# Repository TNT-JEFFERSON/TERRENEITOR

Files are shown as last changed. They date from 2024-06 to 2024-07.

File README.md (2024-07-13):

# `TNT` - `TERRENEITOR`

## About

This repository provides information and knowledge regarding the current progress, evolution, and development of our self-driving robot vehicle for the World Robot Olympian (WRO) 2024 competition in the category Future Engineers, which is build and coded by us.

## TNT & Terreneitor - WRO 2024 Future Engineers

The name of our team is TNT, we chose this name because we will _explode_ the comptetition with our hard work and dedication! On the other hand, Terreneitor is the name of our autonomous robot, build by using lego and arduino together. We are a group of Venezuelan high schoolers who yearn to learn and be masters in robotics. TNT also have plenty of objectives like:

* Obtain expertise and mastery in robotics, engineering and self-driven robots.
* Learning how to cooperate and work as a team to solve problems with ingenious, imaginative, and creative solutions.
* Acquire knowledge regarding new and old technologies, information about eletronics, hardware, software, and more.
* Gain experience for opportunities or competitions that we might face in the future.
* Win the competition and enjoy the process through this exciting road!

TNT is form by three members (all 15 y.o.):

  - Raffaella Salama Arias
  - Emiliana Raquel Guerrero Fermíns
  - Nicola Pasquale Simone Perdomo

One thing that defines us, TNT, is that unlike others, we _don't_ give up easily, we are determine to be the best and improve as much as possible, always looking for success and enjoying every part of the process. You can see this characteristic about us being really strong during "our journey, process and prototypes" below and in the `Older versions of our final robot` folder.

## Content

- `Pictures (Team and vehicle)`: contains photos of the final robot from different views and angles. And photos of us individually and in group.
- `Older versions of our final robot`: contains photos of our previous ideas and prototypes that eventually lead to the final design and robot, Terreneitor.
- `Obstacle management`: contains the source code of the prototypes and the final robot with detailed comments, strategies, flowchart diagrams and pseudocode.
- `Videos`: contains links to our Youtube videos which show how our previous attempts turn out and function, and also how the final robot completes the challenges and more. 
- `Mobility management`: contains all the 3D printed models we used throught our journey, all the lego pieces, electrical components, and materials used in the final robot, a brief discussion regarding the vehicle chassis design/selection as well as the mounting of all components to the vehicle chassis/structure, and more.
- `Power and sense management`: contains power and sense management about the power source for the vehicle as well as the sensors required to provide the vehicle with information to negotiate the different challenges, the reasons for selecting various sensors and how they are being used on the vehicle together and a wiring diagram with BOM that includes all aspects of professional wiring diagrams.

## Materials and components

What is Terreneitor made of? Terreneitor is made of pieces and blocks from pieces and lego parts from diverse lego sets we found in our robotics laboratory, while also using "ready to go" electrical components. We also used an Arduino board as our main controller, since this is what we learned in our school.

|THE LEGO PIECES OUR ROBOT USES ARE:|THE ARDUINO/ELECTRICAL COMPONENTS OUR ROBOT USES ARE:| 
|---|---|
|6x Yellow 4265c|1x MicroServo 9g (SG90)|
|10x Gray 3713|1x Yellow 9V Geared Dc Motor|
|33x Black 2780|1x Gray 5V Dc Motor|
|1x Red 6538c|1x Pixycam 2.1|
|1x Gray 60483|2x Ultrasound sensors|
|2x White x346| Arduino cables |
|2x Red 44809|2x Bateries|
|2x Black 32270|1x Arduino Uno Board|
|1x Blue 32523|1x Protoboard|
|1x Gray 32523|
|4x Gray 32073|
|1x Black 33299|
|4x Gray 32140|
|1x Gray 44294|
|2x Black 3707|
|2x Gray 48989|
|4x Dark gray 3648|
|4x White 40490|
|5x Gray 40490|
|6x Gray 64179|
|4x Grey 56908|
|4x Black 41897|

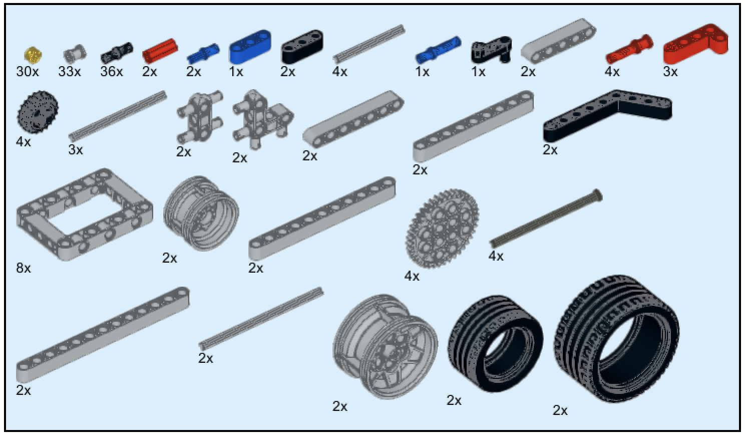
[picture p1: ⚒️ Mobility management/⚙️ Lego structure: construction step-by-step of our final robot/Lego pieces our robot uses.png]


### To know the complete list of all the materials used visit the `Mobility management` folder.

## Our journey, progress and prototypes

In the beginning of our journey, we had plenty of various and diverse ideas on how to build our robot but eventually it all worked out. When we first started, we did messy sketches and tried a lot of ideas. Here are some of our first sketches and ideas for Terreneitor:

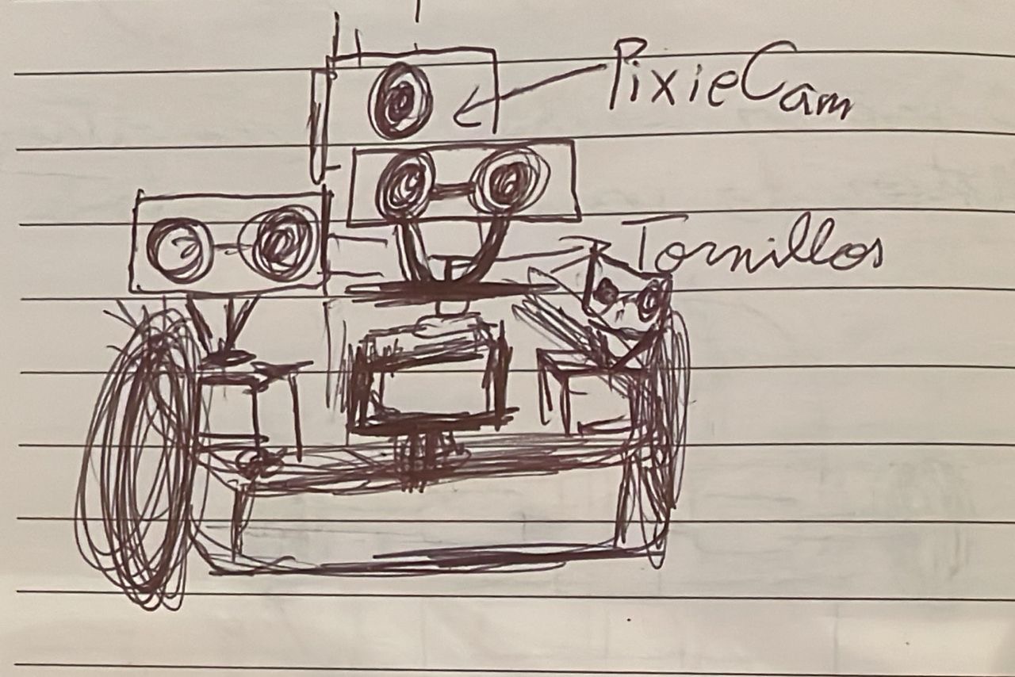
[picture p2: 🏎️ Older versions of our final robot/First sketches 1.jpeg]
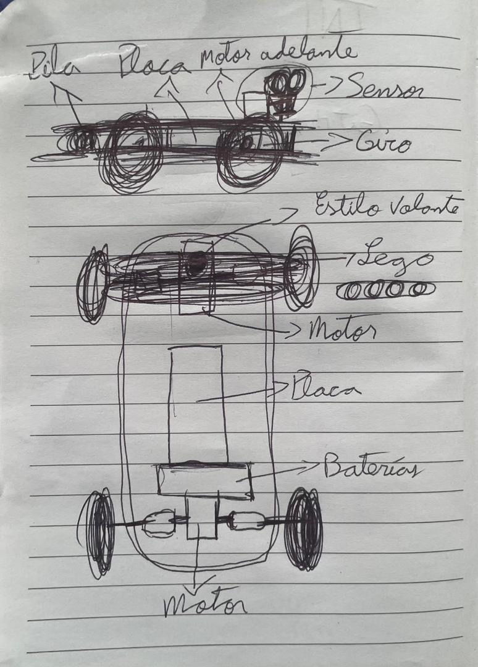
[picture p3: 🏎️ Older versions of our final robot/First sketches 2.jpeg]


Eventually, with these sketches in mind, we started working on the physical robot. We had high hopes for our first prototype, and the more we worked on it, the more our hopes grew. But, there was a problem, a big one...if you see "First prototype wheels mechanism" (you can find in the `videos` folder) you might think, like us, that it would be super fast on the ground, however when we finally were ready to put it to the test... it failed. The wheels mechanism of this prototype did not work on the ground. We tried to change many things and pieces in this prototype to see if it would help, but all our work was in vain, the mechanism still did not work on the floor. Eventually, we find out the cause... the mechanism didn't work because the dc motor that we were using, eventhogh it was fast, it didn't have enough strength and power to move the gear mechanism (the robot was also really tall and heavy causing the dc motor to be carrying this weight all the time, since it was located on the lower part of it. Let's not forget to comment that, also the mechanism for the direction of the robot did not work out too because the motor couldn't move the mechanism (for a better visual understanding visit the `videos` folder), although that was a minor problem compare to the wheel mechanism problem.

But, not everything went wrong with our first prototype because we also did a circuit for the servomotor and for the wheels, and we had a base (constructed by us with lego). All of this things helped us, along with our previous mistakes, to improve and create our second prototype.

In our second prototype, since we learned from our failures and errors from the past prototype, it didn't had any enormous problem, however, there were still problems to be fixed. We realized that the two dc motors we had weren't working simultaneously, which violated the rules of the WRO 2024 competition and also that, eventhough the mesurements of the robot were good according to the rules, it was still, to big in width, which lead to problems like being too heavy so it went super slow (which you can see in the video "Second prototype on the track" in the `videos` folder). And a third
problem was that when we building this prototype was that it did not direct the robot correctly because the wheels of the front couldn't rotate to either left or right. 

As you can realize by now we had plenty of problems since the beginning, let's gather all of them:

### First prototype:

- The wheels mechanism did not work on the ground
- The direction mechanism did not work
- Heavy
- Tall

### Second prototype:

- The mechanism we were using for the wheels violated the rules of WRO 2024 competition
- Too big in width
- Too heavy
- Slow, due to the two previous problems
- Didn't direct the robot correctly

### *(to learn more about our sketches and prototypes go to the `Older versions of our final robot` folder)*

### Final robot

Journies have downsides and good times, advantages and disavantages. After the first and second prototype you might think that because of all this problems we might give up, but contrary to this hypothesis, we didn't (after all "third time's a charm", right?), instead we improved and our mistakes made us stronger, wiser and smarter. So when we created our final robot, we made sure to not make any of our previous mistakes, being very causious in its construction. Thanks to this, we have a robot that is:

- Light weighted
- Short and thin
- The direction and wheel mechanism do work
- Fast
- Doesn't violate any rules of the WRO 2024 competition.

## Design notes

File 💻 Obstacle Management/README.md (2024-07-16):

# Obstacle management

In this directory you will find:
- the software we used to make our code
- all the code we used for our prototypes and the final robot
- our source code with detailed comments
- our pseudo code
- all the strategies our robot uses in order to complete the open challenge round and the obstacle challenge round
- our old and new flowchart diagram 

## Software

The software we used for coding and programming our robot, Terreneitor, is _Arduino Integrated Development Environment (IDE)  _ application version: 2.3.2 in MacOS. Arduino uses a variant of the C++ programming language. The Arduino Integrated Development Environment or Arduino Software (IDE)  contains a text editor for writing code, a message area, a text console, a toolbar with buttons for common functions and a series of menus. It connects to the Arduino hardware to upload programs and communicate with them. We chose using this software not only because of its simplicity but because it what we learned in our school.

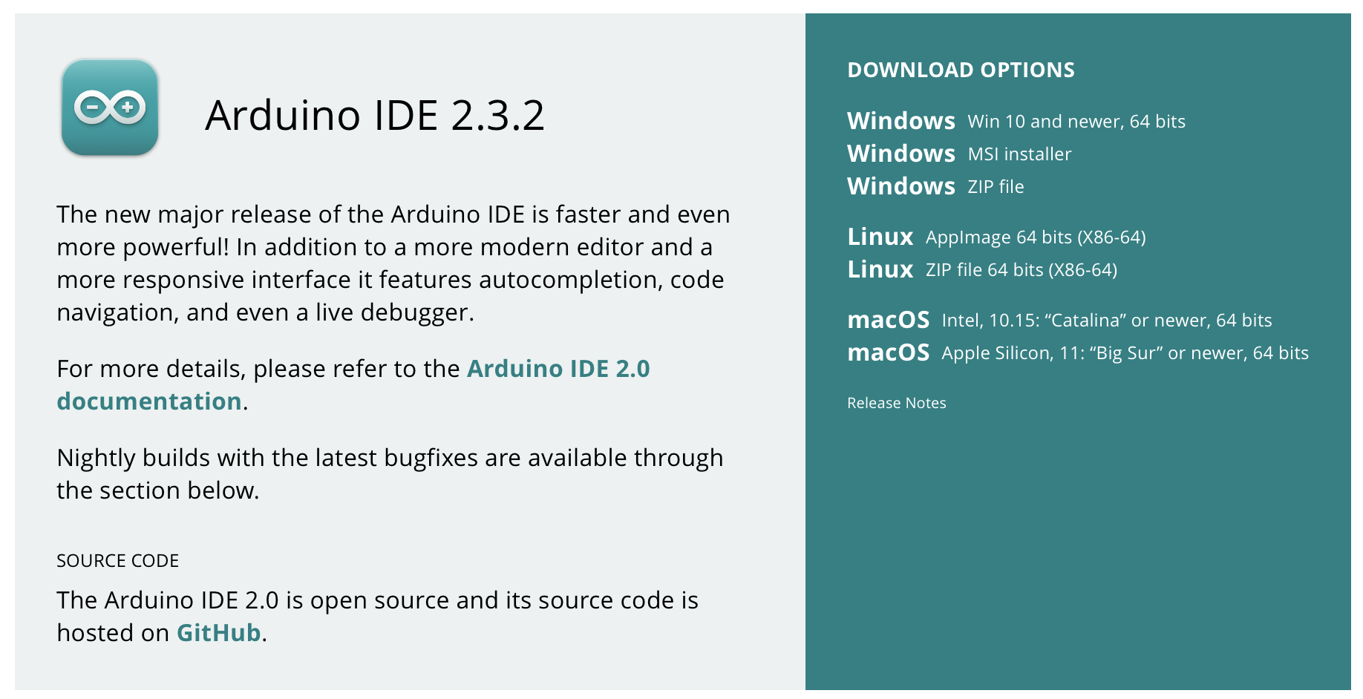
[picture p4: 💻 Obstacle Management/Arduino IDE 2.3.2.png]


##  Pseudocode and strategy

A pseudocode is a representation of code used to demonstrate the implementation of an algorithm without actually doing so. It often acts as a rough draft of coding projects, and is written in an explainable manner to be understandable by programmers at any knowledge level. Meanwhile, a strategy, in this case, is our plan to achieve our goals during the challenges and rounds of the WRO 2024 future engineers competition. Here is our pseudo code and strategy explained in detailed for each round:

### Round 1:

-  The dc motors starts and the car begins to go forward.
-  It continues going straight forward until the pixycam detects an orange or blue line in the track.
-  If the line it sees is orange, it will turn to the right.
-  If the line it sees is blue, it will turn to the left.
-  While the pixycam is working, the ultrasonic sensors in our robot are working too. These ultrasonic sensors help us know the distance between our robot and the walls in the track.
-  If the left wall is closer to the robot than the right wall, it turns to the right side, if not, then the right wall is closer to the robot than the left wall, it turns to the left side.
-  After the robot sees the orange line and/or blue line and turns 12 times (makes 3 laps) it stops where it started and the round ends, if it doesn't sees the orange line and/or blue line and turns 12 times (makes 3 laps) it constinues going until the 3 laps are completed and the round/challenge ends.

### Round 2:

-  The dc motors starts and the car begins to go forward.
-  It continues going straight forward until the pixycam detects an orange or blue line _or_ a green or red obstacle in the track.
-  If the line it sees is orange, it will turn to the right.
-  If the line it sees is blue, it will turn to the left.
-  If the obstacle it sees is red, it will turn to the right.
-  If the obstacle it sees is green, it will turn to the left.
-  While the pixycam is working, the ultrasonic sensors in our robot are working too. These ultrasonic sensors help us know the distance between our robot and the walls in the track.
-  If the left wall is closer to the robot than the right wall, it turns to the right side, if not, then the right wall is closer to the robot than the left wall, it turns to the left side.
-  After the robot sees the orange line and/or blue line and turns 12 times (makes 3 laps) it stops where it started and the round ends, if it doesn't sees the orange line and/or blue line and turns 12 times (makes 3 laps) it constinues going until the 3 laps are completed and the round/challenge ends.

### Round 3:

** In this round, the robot works the same the only step that changes in the final step in which the car has to park inside a magenta parking lot. **

-  The dc motors starts and the car begins to go forward.
-  It continues going straight forward until the pixycam detects an orange or blue line _or_ a green or red obstacle in the track.
-  If the line it sees is orange, it will turn to the right.
-  If the line it sees is blue, it will turn to the left.
-  If the obstacle it sees is red, it will turn to the right.
-  If the obstacle it sees is green, it will turn to the left.
-  While the pixycam is working, the ultrasonic sensors in our robot are working too. These ultrasonic sensors help us know the distance between our robot and the walls in the track.
-  If the left wall is closer to the robot than the right wall, it turns to the right side, if not, then the right wall is closer to the robot than the left wall, it turns to the left side.
-  After the robot sees the orange line and/or blue line and turns 12 times (makes 3 laps) it searches for the magenta parking lot with the pixycam and  parks inside it and the round ends, if it doesn't sees the orange line and/or blue line and turns 12 times (makes 3 laps) it constinues going until the 3 laps are completed and it parks inside it and the round/challenge ends.

In order to explain all of the above better, we designed a flowchart diagram, a visual representation that depicts our process, system, computer algorithm, and a brief summary of how our code of the robot works on the track. During our journey we created two flowcharts as you can see below. The difference between the two diagrams is that the old one wasn't a good flowchart and didn't completely follow all the rules of a flowchart diagram and didn't explained correctly how our code and process works, on the other hand, our new flowchart diagram, does follow all the rules and conditions of a new flowchart diagram and explains correctly how our code and process works.
 
(both diagrams were created entirely by us, TNT, using the smartdraw website: https://www.smartdraw.com/flowchart/flowchart-maker.htm)

|Our old flowchart diagram|
|--------------------------|
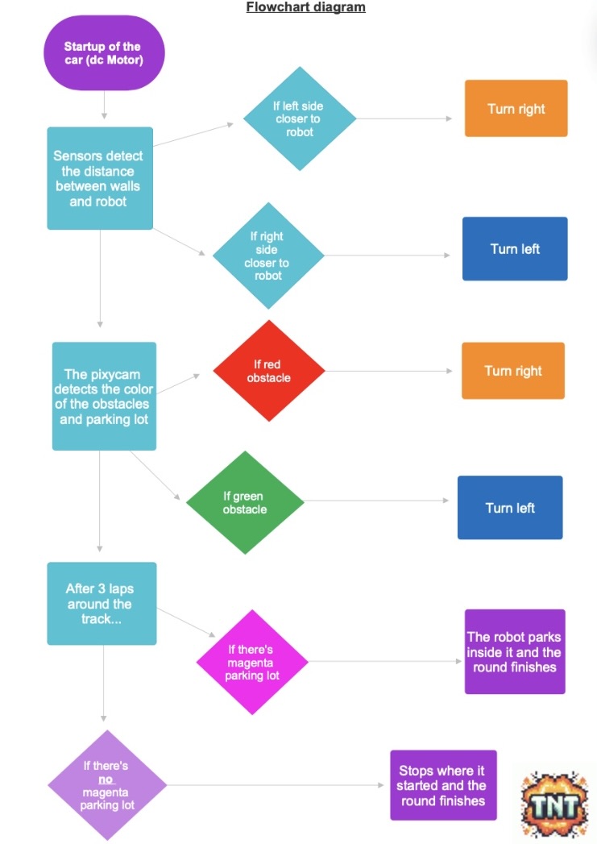
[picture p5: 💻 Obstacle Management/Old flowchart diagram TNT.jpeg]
||

|Our new flowchart diagram|
|-----------|
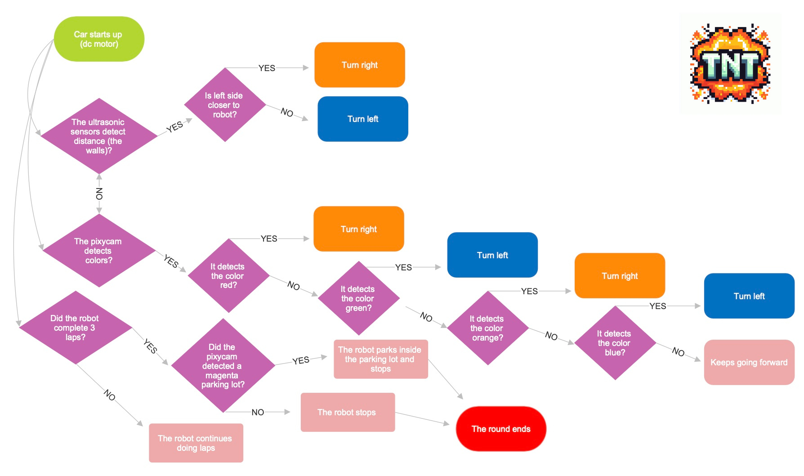
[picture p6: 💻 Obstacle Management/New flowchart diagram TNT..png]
||

In this directory we uploaded all the codes we used both for our prototytpes and the final robot. All of this source codes contain detailed comments, so make sure to check them thoroughly!

Below you have a brief summary, pseudocode and strategies used in each indivual file and code:

## Code for first round (Open challenge round)

This code works for the first round, if you want to know what it is about check the file in the folder that's named "First round.ino", since the detailed comments will tell you what it is about.

## Code for first round 2 (Open challenge round)

This code works for the first round, if you want to know what it is about check the file in the folder that's named "First round.ino", since the detailed comments will tell you what it is about.

## Code for second round (Obstacle challenge round)

This code works for the second round, if you want to know what it is about check the file in the folder that's named "Second round.ino", since the detailed comments will tell you what it is about.

## Below you'll see some _tests_ codes we did before:

## Code for the motors of the second prototype:

- What this code does is simple: 

   - First, it takes 2 seconds to start the code, this is made intencionally so we had to accomodate the robot in the track            comfortably.
   - Second, the code starts and it turns both motors on, making it go in a straight line for 14 seconds
   - After the 14 seconds have passed, the robot turns to the side for 9 seconds (by turning off one motor while the other one is still on)
   - And finally, it goes in a straight line again (turning on both motors, like in the beginning).

The robot does this cicle 4 times,for it to finish that round, which is the first challenge (the open challange). This code is a way of completing the first challenge by using time.

- You can see this code being used and putted to the test in "Second prototype on the track" (in the videos folder).

## Code for the three ultrasonic sensors:

- This code is so the three ultrasonic sensors work together in unison. The sensors perceive the distance in cm in this code.
- This code also works together with the servomotor code.

## Code for the servomotor and ultrasonic sensors:

This code makes the direction mechanism and the three ultrasonic sensors in our robot work together

It works like this:

- If the robot detects that one side is more than 50cm it goes that way
- If the robot detects that one side is less that 50 cm it goes to the opposite way

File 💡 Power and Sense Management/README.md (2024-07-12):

# Power and sense management

In this directory we will talk about:

- the power source for the vehicle
- the sensors required to provide the vehicle with information to negotiate the different challenges
- reasons for selecting various sensors and how they are being used on the vehicle together 
- wiring diagram that includes all aspects of professional wiring diagrams
- Bill Of Materials (BOM)

Terreneitor has two power sources: The first one being a 5000 mA powerbank which provides power to the Arduino Rev3 Board, which is the main controller of our robot. The second one are four rechargable batteries of around 2300-1300 mA each and 1.2V that give power to the dc motor and are connected directly to the protoboard (were it becomes part of our circuit). In order, to turn the batteries (basically the robot) on and off, it counts with a switch (a power controller board) to do this.

These power sources for the vehicle, give power to whole robot, but some really important components that it gives power to are the sensors. Our robot counts with three sensors, two ultrasonic ones and one pixycam 2.1. The ultrasonic sensors help us detect the distance between the robot and the walls and/or obstacles, these two sensors are in the front of our robot. The pixycam 2.1 helps up detect colors in the surroundings of the robot, it helps detect the red or/and green obstacles in the second challenge, the magenta parking lot, the black walls, and the orange and blue lines in the track. 

We chose to have ultrasonic sensors in our robot because since they detect the distance between the robot and the walls/obstacles it helps us know how far or how close the robot is to these things. These is important because if the robot is close to the walls, for example, it turns (you can see these better explained in our code and in the `obstacle management` folder). If our robot didn't had any ultrasonic sensors it would 100% crash with the walls or obstacles in its way and wouldn't complete the challenges correctly. On the other hand, we chose to have a pixycam in the front of the robot, to the detect the colors of the things around the robot, this is also extremely helpful and important because, for example, in the rules of the WRO 2024 competition its established that if the robot sees a red obstacle it has to turn right, if we didn't had the pixycam we wouldn't be able to know the color of the obstacles in the track and would fail the challenge.

As you can see, the sensors are a very important part in the robot and eventhough they consumed a lot of power (because we have three of them) it is super worth it. 

Of course, for pracmatiqueness and better efficiency, the sensors and the power sources are not connected directly to the our main controller, the Arduino Rev3 Board, instead, they are connected to a circuit which then connects to the board. For you to know what our circuit looks like and how it works we made a wiring diagram that includes all aspects of professional wiring diagrams, for a better comprehension:

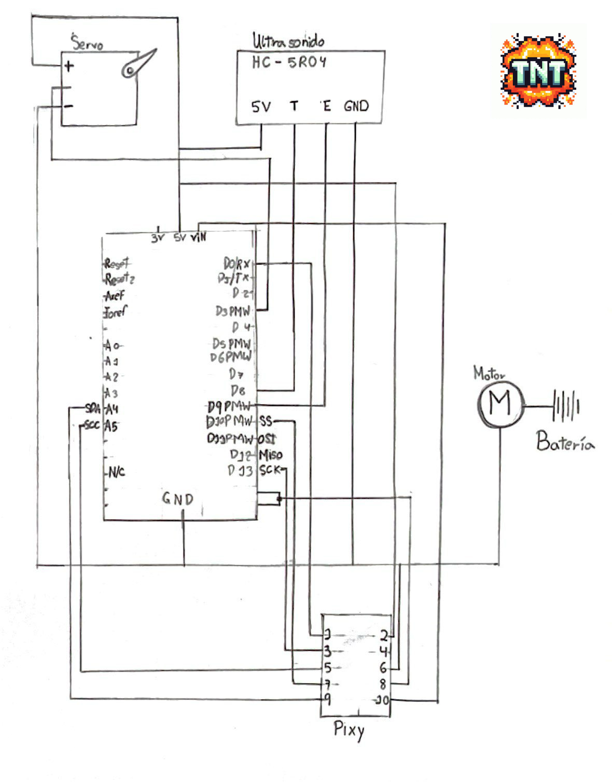
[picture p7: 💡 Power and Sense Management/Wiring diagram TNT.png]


The sensors and the power sources are not the only components and pieces we used in our robot, and are not the only important and expensive parts we used, so we also elaborated a Bill Of Materials (BOM). Below you can see it:

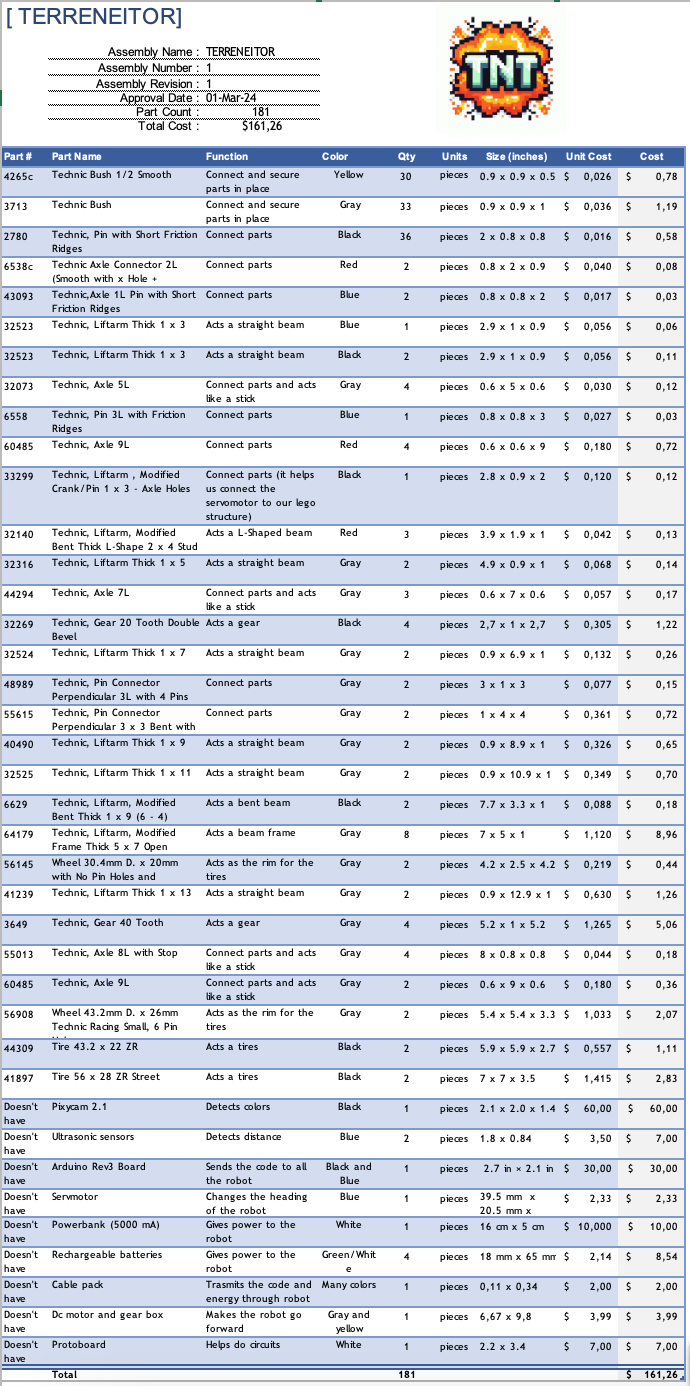
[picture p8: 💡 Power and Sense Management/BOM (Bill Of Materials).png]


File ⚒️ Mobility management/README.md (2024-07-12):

# Mobility management

We chose a vehicle chassis that was open and that would allow us to have both an Arduino board, a protoboard and a power source connected, which is why it was necessary to create two floors because otherwise the car would be very long and would exceed the measurements provided. We made two floors with simple Lego structures and made some small adaptations to place our DC motor, place our battery and 3D printed our own piece to be able to mount the pixy camera.  

We chose a 3V DC motor, which is one of the most common, but seeing that it did not have enough power, we worked with the “large gear-small gear” principle (to increase the speed of the output the driver gear is larger than the driven gear which is small (this will increase the speed of the output but decrease the “torque”)), which is what you will see in the diagram of the gear box and our propulsion, then with that engine, we simply place gears at the end of it, to double what is the angular speed and the linear speed that is generated on what are our rear wheels. That generates a little instability if we do it with a single gear, therefore we place two gears on each side, not to generate more power, but to generate more stability. 

We are working with 5000 mA batteries that are commercially known as “powerbanks” precisely because they give a stable current through a USB cable that will not bend or break and will allow us to constantly power our vehicle, we also use four rechargable batteries of around 2300-1300 mA each, to power our robot. (to see this explained in more detail check the `power and sense  management` folder)

For the direction, we had to use a servomotor, it would have been ideal to place another 3V DC motor for this function, however, we would have had to work a lot with the voltage variations to have to make the change between forward and backward, that would require an additional integrated chip which would congest too much work for us on a physical level, therefore we placed a servomotor to work directly with the code which would allow us 90 degree rotations to the right and to the left and This is attached directly to a simple connection shaft and is what gives us mobility to the left and right of our vehicle. 

For the main controller, we are using an Arduino Rev3 Board, this is because as we mentioned in our introduction, we are high schoolers, and in our school we learned how to use this board. And also that the final proyect for our seniors in robotics is the "Smars" proyect, which is about constructing a autonomous robot (of course, this robot does nothing similar to the goals and purposes of this competition, but it inspire and gave motivation for this category). Not only that, but an Arduino board is easier to learn than other boards and controllers.

Here is our scheme of conduction and direction of our robot:

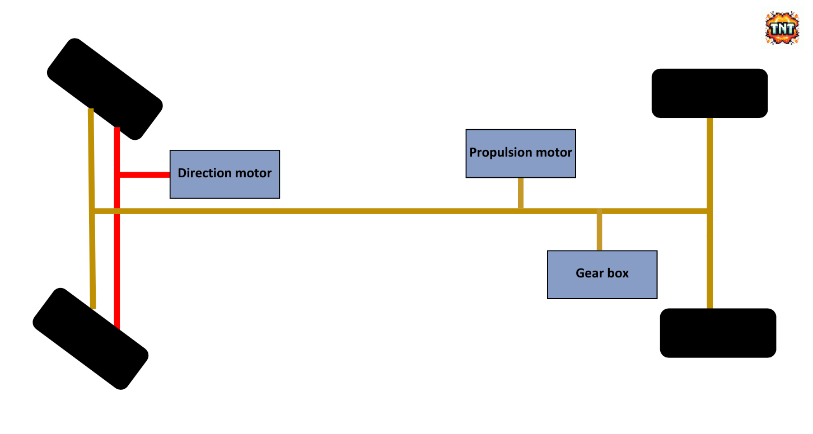
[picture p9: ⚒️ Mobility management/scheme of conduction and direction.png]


# Build

Now we will talk about, what our robot is made of: all the lego pieces, "ready to go"electrical components, and materials used in the final robot.

What is Terreneitor made of? Terreneitor is made essentially of:
- Pieces and lego parts from diverse lego sets we found in our robotics laboratory
- While also using "ready to go" electrical components  
- And our own parts and materials like personalized 3D printed models, silicone, tape and zip ties
- Also, the main controller of our robot is an Arduino board

In the chart below titled "THE LEGO PIECES OUR ROBOT USES ARE:", you will find:
1) First, the amount of that especific piece we used on the robot
2) Second, the color of that lego piece
3) Third, the code of that lego piece

|THE LEGO PIECES OUR ROBOT USES ARE:|                             
|-----------------------------|
|6x Yellow 4265c|
|10x Gray 3713|
|33x Black 2780|
|1x Red 6538c|
|1x Gray 60483|
|2x White x346| 
|2x Red 44809|
|2x Black 32270|
|1x Blue 32523|
|1x Gray 32523|
|4x Gray 32073|
|1x Black 33299|
|4x Gray 32140|
|1x Gray 44294|
|2x Black 3707|
|2x Gray 48989|
|4x Dark gray 3648|
|4x White 40490|
|5x Gray 40490|
|6x Gray 64179|
|4x Grey 56908|
|4x Black 41897|

You can see all of the lego pieces we used, for a better comprehension, more clearly and neatly in this materials chart:

(this materials chart is made by us using the official lego _BrickLink_ app)



To know about how we build the lego structure step-by-step check the `⚙️ Lego structure: construction step-by-step of our final robot` directory which you will find in this folder.

In the chart below titled "THE "READY TO GO" ELECTRICAL COMPONENTS OUR ROBOT USES ARE:", you will find:
1) First, the amount of that especific piece we used on the robot
2) Second, the name of that "ready to go" electrical piece/component

|THE "READY TO GO" ELECTRICAL COMPONENTS OUR ROBOT USES ARE:|Photo of each:| 
|---|---|
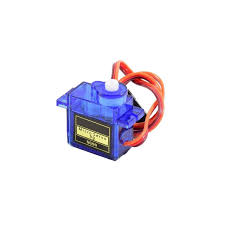
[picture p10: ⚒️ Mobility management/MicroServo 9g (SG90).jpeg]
|1x MicroServo 9g (SG90)||
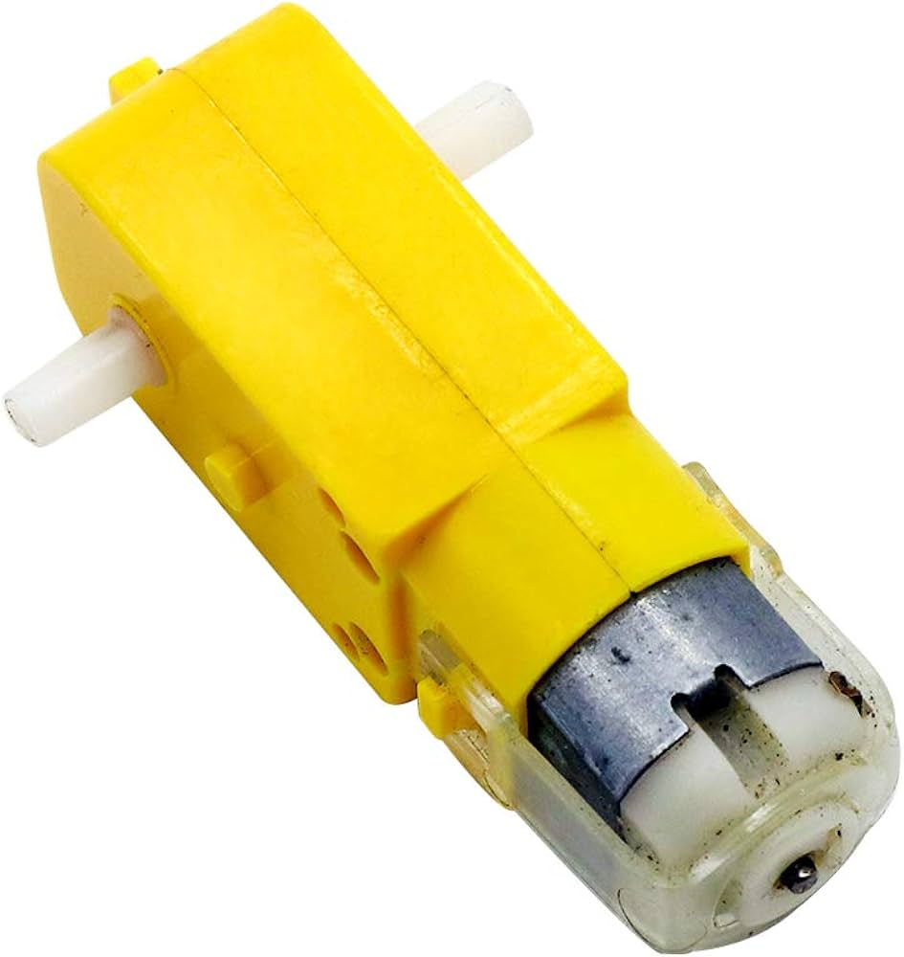
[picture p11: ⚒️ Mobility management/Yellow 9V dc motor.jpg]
|1x Yellow 9V Geared Dc Motor| |
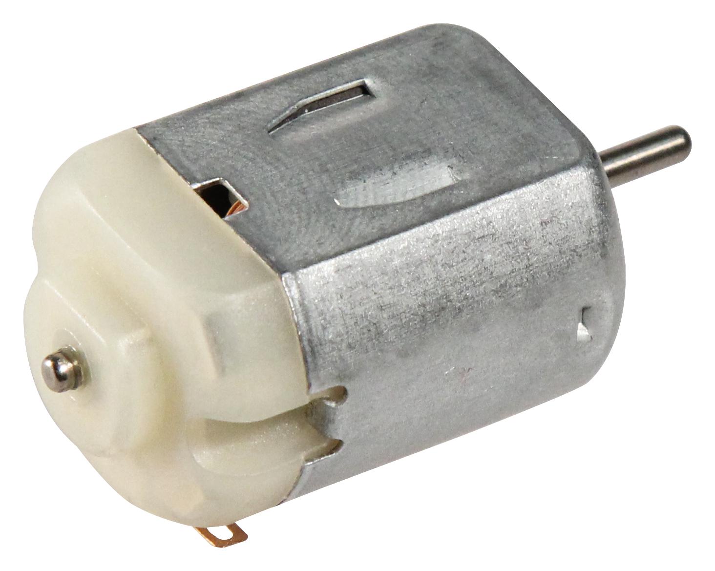
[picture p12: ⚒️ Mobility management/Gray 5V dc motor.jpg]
|1x Gray 3V Dc Motor| |
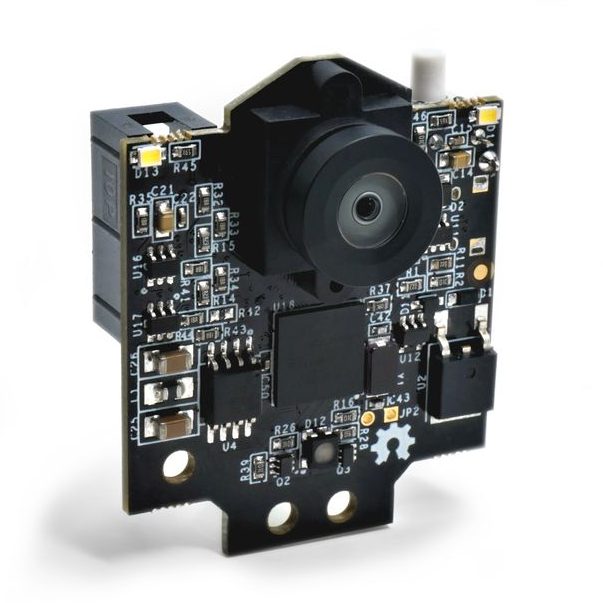
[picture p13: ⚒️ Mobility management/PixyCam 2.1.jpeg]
|1x Pixycam 2.1||
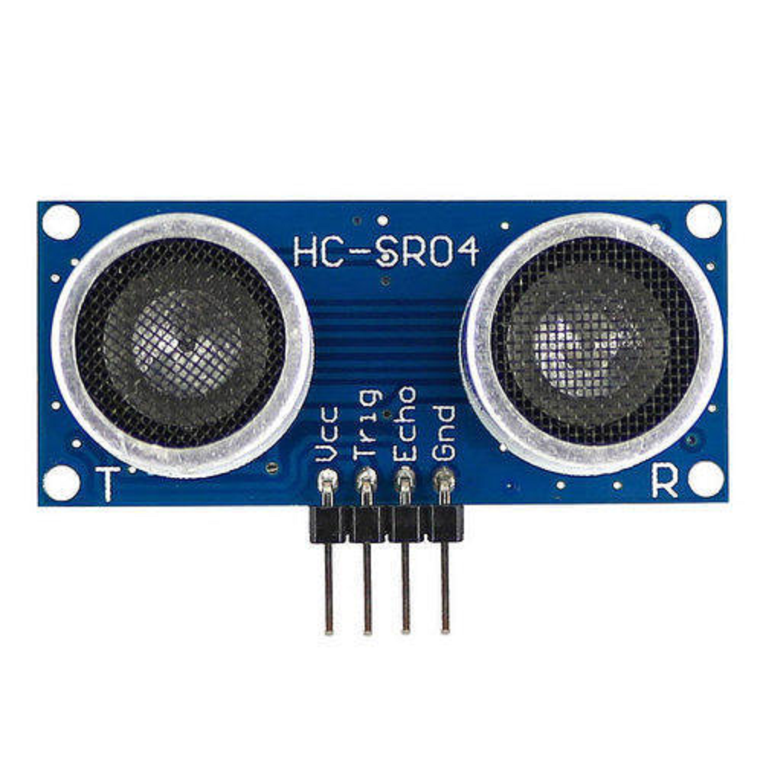
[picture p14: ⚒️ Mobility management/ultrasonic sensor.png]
|2x Ultrasonic sensors||
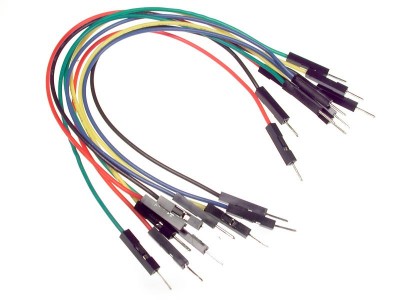
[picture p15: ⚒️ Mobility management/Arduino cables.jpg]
|A lot of Arduino cables| |
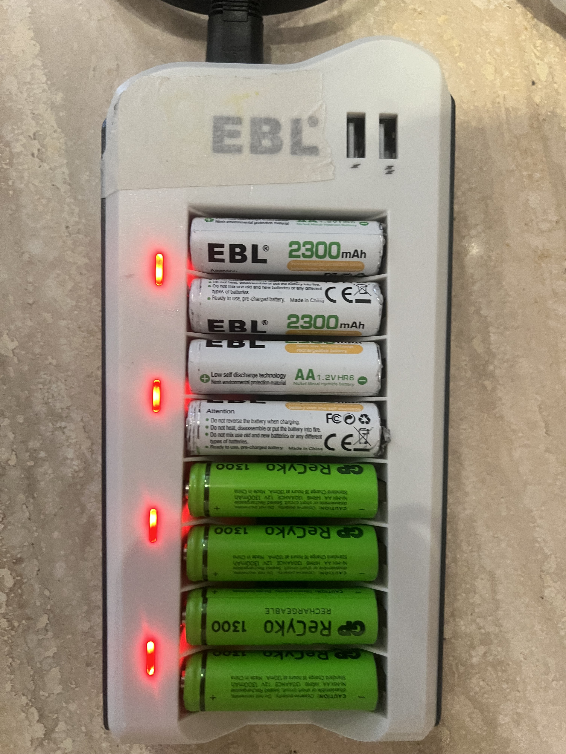
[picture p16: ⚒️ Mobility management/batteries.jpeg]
|2x Bateries|  |
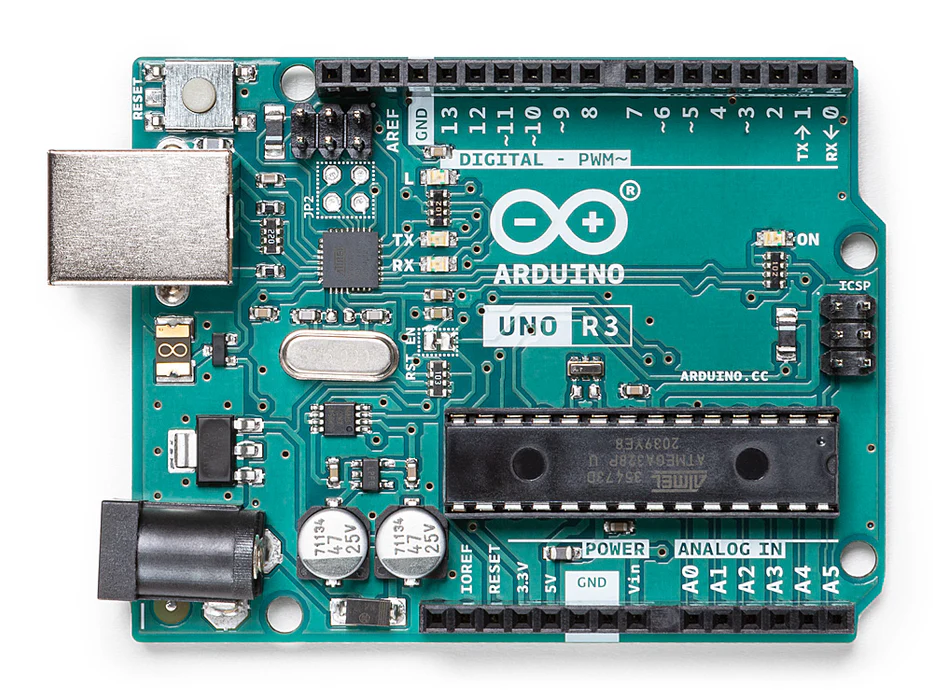
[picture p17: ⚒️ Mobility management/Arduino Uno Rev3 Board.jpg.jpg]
|1x Arduino Uno Rev3 Board||
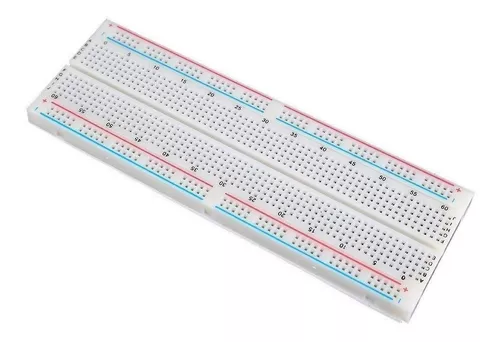
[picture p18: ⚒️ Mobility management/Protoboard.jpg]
|1x Protoboard MB-102 830 pins||

Apart from lego pieces and "ready to go" electrical components, we also used ordinary and our own materials, components and pieces like:

- our own 3D printed models (which you can find in this folder the files, and below the explanation)
- ordinary adhesive materials to join things or make them stronger like:
  - silicone
  - blue/black tape
  - zip ties

|OTHER MATERIALS OUR ROBOT USES ARE:|Photo of each:| 
|---|---|
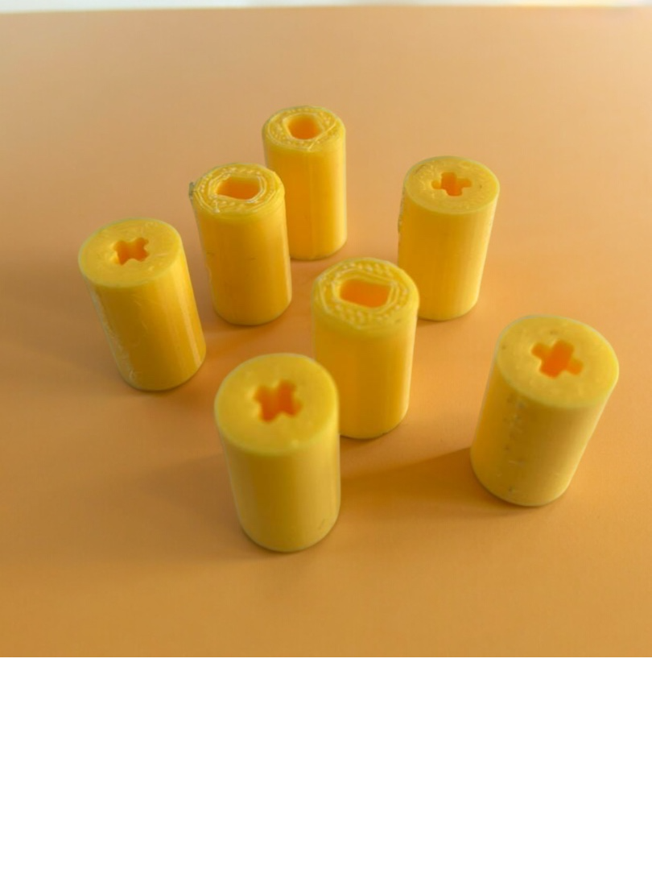
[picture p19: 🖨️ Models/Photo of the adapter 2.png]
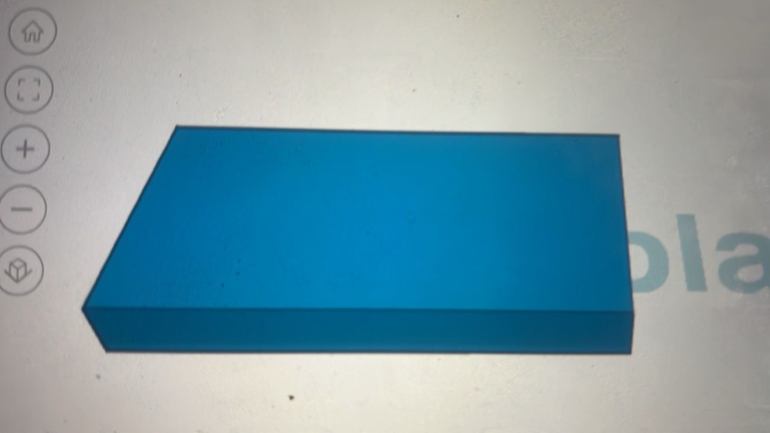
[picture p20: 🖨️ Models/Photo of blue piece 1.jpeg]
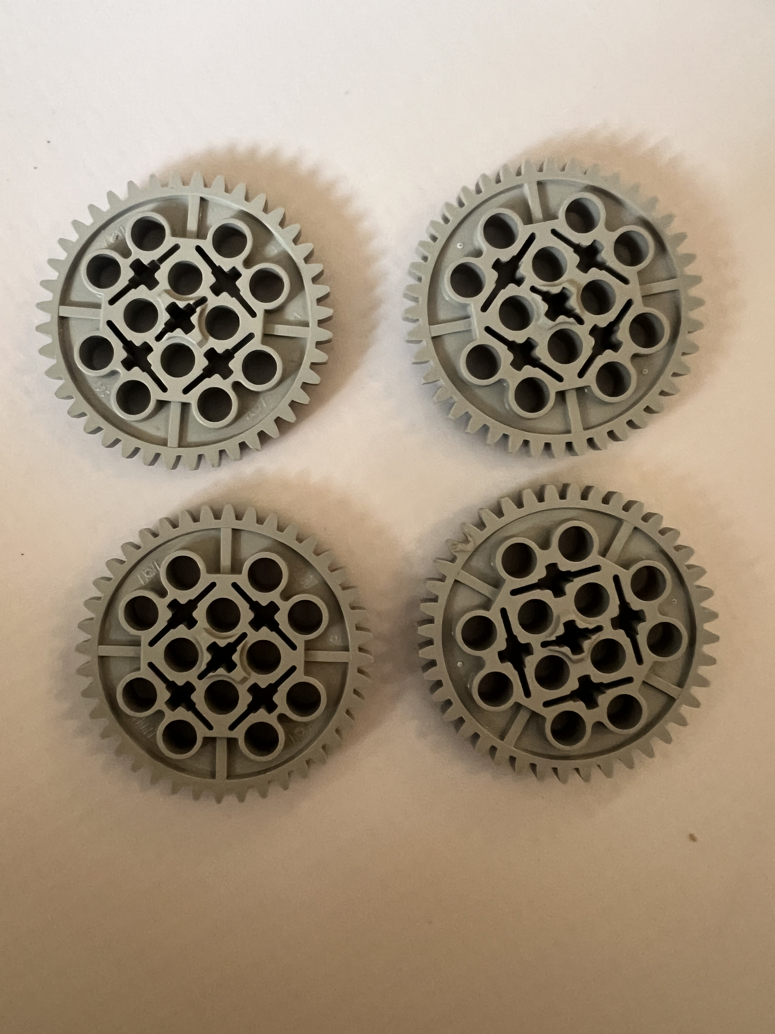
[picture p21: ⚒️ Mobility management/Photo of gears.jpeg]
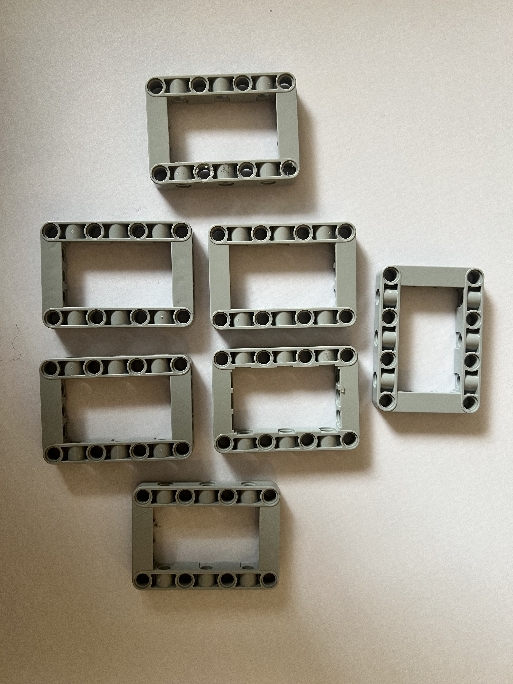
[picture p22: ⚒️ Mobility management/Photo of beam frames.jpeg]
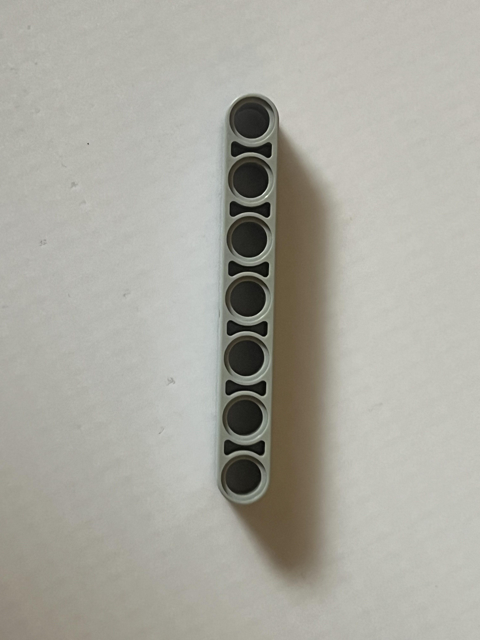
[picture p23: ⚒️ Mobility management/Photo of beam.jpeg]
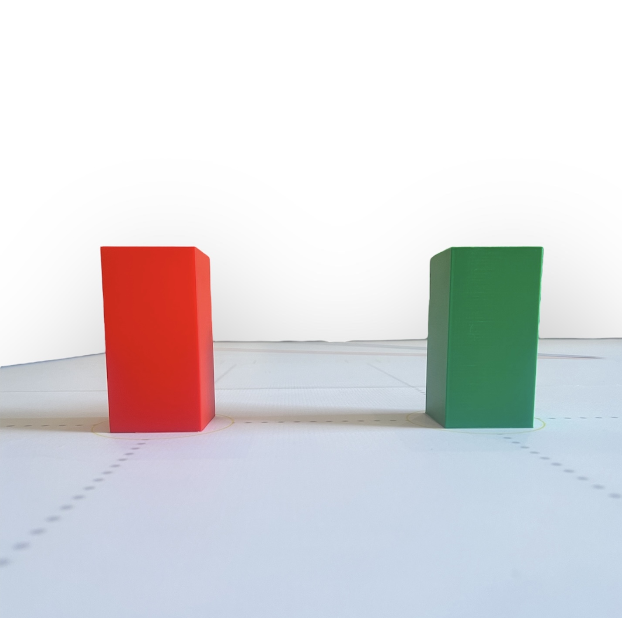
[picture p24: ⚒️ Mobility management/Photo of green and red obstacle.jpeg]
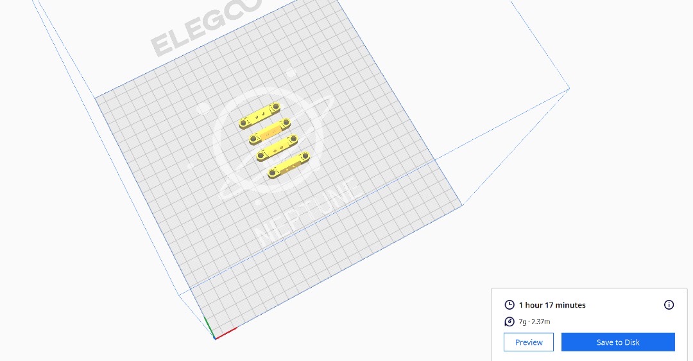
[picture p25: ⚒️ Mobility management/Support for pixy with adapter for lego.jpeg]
|3D printed models||
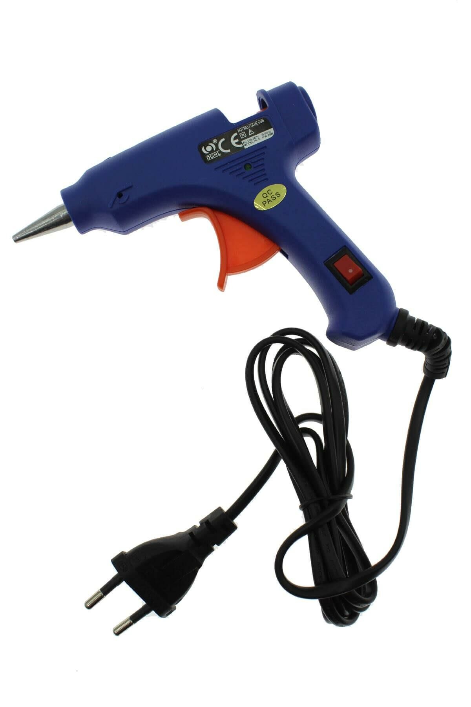
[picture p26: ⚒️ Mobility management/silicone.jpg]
|silicone| |
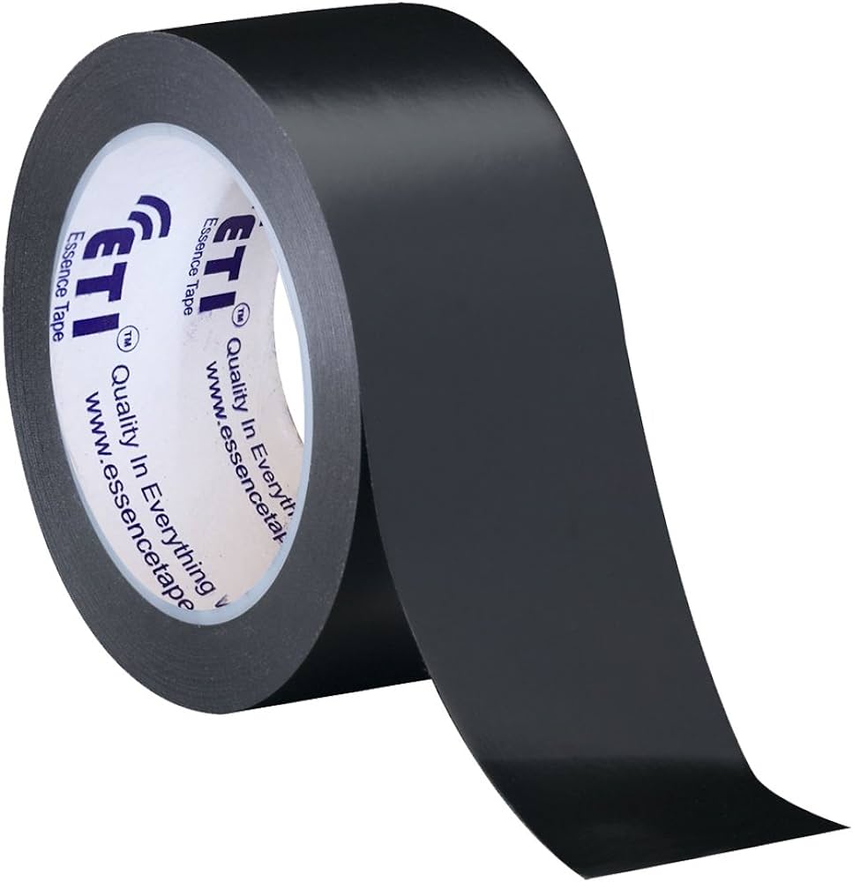
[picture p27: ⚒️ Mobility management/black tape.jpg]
|black/blue tape|  |
|zip ties||

## Why did we chose all of these previous materials?

We chose all of these previous materials, components and pieces in our robot because is what we found in our robotics laboratory and school and is also what we are being taught.

Absolutely everything (the diverse lego pieces, the "ready to go" electrical components, and more) were also bought here in our country, Venezuela, except for the pixycam which was imported from abroad.

## Note:

- Mostly eveything we just mentioned is part of our final robot, but for the previous attempts and prototypes we used the same or almost the same materials, pieces, parts and components.

# Models

Now, we will talk about all the information regarding our 3D printed models, designed and printed by us. 

# 3D Scanner

Its important to mention that we also borrowed a 3D scanner to print some models. This is because in our robotics laboratory we needed to modify some lego pieces, or didn't have enough of them, so we decided to print our own lego pieces.

 

# Our 3D printers

These are the 3D printers we use at our school to print our 3D models, which are a fundametal part in the creation of our robot

 

## Adapter for the wheels

This model is an adapter so we can join together the dc motor and the lego stick. The model has 2 sides: the first one being a cross so the lego stick fits there perfectly and the second one being a line where the dc motor fits. This 3D printed model is an essential part of our final robot's wheel mechanism, since thanks to this model it works.

⇩ ( The blue and yellow parts you see next to the wheels are the adapters ) ⇩
                                                                     

 


### (you can find the 3D model stl document in this folder)

## Support for pixy with adapter for lego

This model counts with two pieces which support the pixy like a case, it also counts with two holes at the ends so it can be adapted to the lego pieces which our robot is made with.

 

### (you can find the 3D model stl document in this folder)

## Blue piece

This model is a piece that functions to stop the dc motor from moving so it has a better performance. This model what 4 cm x 2 cm so it would in the space below the robot in the first prototype. 

 
 

### (you can find the 3D model stl document in this folder)

## Green and red obstacles

This model counts with two pieces: the first one being red and the second one being green. This pieces help us practice for the second round (obstacle challenge).

 
 

### (you can find the 3D model stl document in this folder)

## Beam frames 

This model was made with help of the 3D scanner. This model was created because we didn't had enough beam frames at our robotics laboratory, so we decided to 3D print our own.

 

### (you can find the 3D model stl document in this folder)

## Gears

This model was made with help of the 3D scanner. This model was created because we didn't had enough gears like this at our robotics laboratory, so we decided to 3D print our own. We also modified them to be a little bigger and therefore, function better. It's important to mention that gears are a fundamental part of our wheels mechanism, as you read before.



### (you can find the 3D model stl document in this folder)

## Beam

This model was also made with help of the 3D scanner. This model was created because we didn't had enough beams like this at our robotics laboratory, so we decided to 3D print our own. We also modified them to our needs (we made it shorter). You can see this mean thourghout a lot of our robot's composition.



### (you can find the 3D model stl document in this folder)

## As a final note, it is important to mention that, as you have read, we build Terreneitor from cero, meaning we did _`not`_ use any Standard Construction Kit "Off the shelf" to build our robot. We designed and builded our own original and unique robot, with our own diverse lego pieces and electrical components.

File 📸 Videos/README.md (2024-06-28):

# Videos

In this directory you will find links to:
- Our Youtube channel.
- Videos of our previous prototypes, their circuits, and mechanisms.
- Videos of our final robot's circuits and mechanism.
- Demostrative videos that show our robot completing challenges and showing its speed and velocity.

## First prototype circuit:
- Here we show the whole circuit of our first prototype. It was located at the top of the prototype and was coded and build using Arduino IDE and arduino components.

- https://youtu.be/AXf8ZZWNw28?si=PzxdN1z0rt_WSu8q

## First prototype wheels mechanism:
- Here we demostrate the mechanism of the back wheels of our first prototype and the incredibly fast velocity and speed it had.

- https://youtube.com/shorts/HGfQiTwByXs?si=bKAq2ve8cOI9ZJAf

## First prototype direction mechanism:
- Here we show how the direction mechanism of our first prototype wasn't working (this problem was mentioned in "Our journey, progress and prototypes" in the README of the repository)

- https://youtube.com/shorts/1Q_TQaBaEv4?si=9o6V4hn82UMSl9a6

## Second prototype on the track:
- Here we show how our second prototype was on the track. Though it was very slow, it completed the challenge successfully.

- https://youtube.com/shorts/VP0IJyykLAc?si=gImFBKUhP4l3haT9

## Second prototype's circuit:
- Here we show the circuit of the second prototype

- https://youtu.be/xLu6_tLh33c?si=TgCPNXHQxp1kua-9

## Final robot's direction: 
- Here we demostrate the ability to turn from one side to another (and the mechanism to do so) of our robot:

- https://youtu.be/LIwiXsxAzfs?si=ffl3m8pvXG6mpt3J

## Final robot on the ground:
- Here we demostrate Terreneitor's speed and fast velocity on the ground.

- https://youtu.be/L0IB8tpKi-c?feature=shared

## Final robot's direction mechanism and ultrasonic sensors
- Here we demostrate how the servomotor and the ultrasonic sensors in our robot work in unison

- https://youtube.com/shorts/-ydbWwwqAOM?si=ZDhiF-gVkNM1LRam

## Final robot on the track 
- Here we show the final robot on the track

- https://youtu.be/CYdOAYD9zVA?si=WlyTS36bONAyFMDh

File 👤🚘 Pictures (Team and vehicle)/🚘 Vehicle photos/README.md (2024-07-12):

## Vehicle photos

In this directory, you will find all the photos related to our final robot:
- its circuits
- direction mechanism
- ultrasonic sensors

You can see this things in different angles and views:
- cenital views
- back views
- front views
- side views

(to know about how it works, what its made of, and everything related to our final robot, Terreneitor, check all the folders and READMEs in this repository, except the `older versions of our final robot` folder, which talks about our previous prototypes and attempts, instead of our final robot)

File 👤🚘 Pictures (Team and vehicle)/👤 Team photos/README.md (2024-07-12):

# Team photos

In this directory you will find the photos of:
- each individual member of the team
- a photo of all the team members together

Our team counts with three members. We are:

1) Raffaella Salama Arias



2) Emiliana Raquel Guerrero Fermín



3) Nicola Pasquale Simone Perdomo



### And together we are TNT!



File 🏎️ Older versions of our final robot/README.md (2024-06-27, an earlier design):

 # Prototypes and sketches 

In this directory you will find all the information regarding our previous ideas and prototypes, their avantages and disavantages and the journey that lead to this prototypes. It is important to mention that we are going to focus here on the sketches and prototypes, not on the final robot (if you want to know more about our final robot, check the other folders like:`vehicle photos` folder, the `build` folder, etc. You can also read the README of this repository since we mainly talk about our final robot there and , as mentioned before, in the other folders except for this one).

- Now, _why is there a need to talk especifically about our sketches and prototypes?_

It is a need and an importance to talk about our sketches and prototypes because they have lead the way and gave us an incredible help for our final robot. They have shaped the way our final robot is today. It is important to have this in mind because, if you read "Our journey, progress and prototypes", you will see how it was a journey that started with a lot of downfalls but eventually we realized to learn from our mistakes and we recovered, making Terreneitor, our final robot.

## Sketches

Before we even started building the robot, we had a clear vision for what we wanted our robot to be like. We wanted a robot with 2 or 3 ultrasonic sensors (especially 2 in the front), the pixycam in the middle of the front of the robot (between the 2 ultrasonic sensors), to have 4 wheels (2 in the front, and 2 in the back like a real car), use 1 dc motor to move both back wheels, and have the batteries and arduino board behind the sensors (in the middle of the base). In the sketches below you can see these ideas reflected:

     

## First prototype

After making the sketches for what we wanted our robot to look like, we started the construction by using lego pieces from the _MINDSTORMS education EV3_ lego set. As mentioned before, we wanted the both of the back wheels to move by using 1 dc motor who would move them simultaneously. 

### Step 0.1: 

In the beginning, we made the base really long, as you can see in the image below, but if you watch closely, you'll see at the end of the robot, the mechanism for the wheels which is mainly made by using gears (if you want to see how this mechanism works check the `videos` folder). On the other hand, in the front of the robot you'll see the direction mechanism which we later changed.



### Step 1:

After realizing it was too long, we shorten it as you can see in the photo below. You can also see the direction mechanism more clearly and see how we connected the dc motor to the wheels mechanism (when the motor was on, it moved the gray lego adapter who moved the gears and finally made the wheels move in unison, at the same time (this wheel mechanism didn't work on the ground because the dc motor didn't have enought strength and power to move the mechanism, plus the weight of all the robot was on top of it).



### Step 2:

In step 2, we changed the direction mechanism of the robot, opt in for a gear-based mechanism. You can also see how in this mechanism to move the gear we were using a dc motor instead of a servomotor.



### Step 3:

Here, you can see the direction mechanism mentioned in step 2 more clearly, this mechanism was supposed to work like this: The big gear moved the black piece below, making it go to either side. This mechanism, did not work (as you can see in the `videos` folder) because the gear wasn't strong enough to move the black piece, and another problem with this mechanism was that since we were using a dc motor instead of a servomotor it would move only to one side. You can also see how tall and big it has making it really heavy.



### Step 4:

In step 4, you can see the wheels mechanism from below the robot, you can see the gears, dc motor, and everything that belongs to this mechanism. 
You can also see the direction mechanism from below. And that we were using two small wheels in the front, and two bigger ones in the back.



### We learned many things from this prototype:

- It was heavy
- It was tall and big
- To not used a gear based direction mechanism
- Use a servomotor in the direction mechanism instead of a dc motor
- To use a simplier and light weight wheel mechanism so the dc motor can can power and make move on the ground

## Second prototype

After we realized all the big problems our first prototype had, we decided to start again and build another prototype.

In the two pictures below, you can see how we applied our inical ideas we thought in the sketch: putting 2 ultrasonic sensors in the front of the robot and in between the pixycam. But if you see closely, you will see that it had no servomotor nor direction mechanism. So when the robot had to turn, one motor would be turn off and the other one will still be on, making it turn and they it would straight in a line and both motors will be turned on (if you want to know more about how this works check the `code` folder)

 

However, there was another problem, in the two images below you can see that for this prototype we had two dc motors, each one working for each wheel, but this violated the rules of the WRO 2024 competition so we had to change it eventually. You can also see the cicuit and how wide and big it was, which lead to the robot being very slow (you can see this in the `videos` folder)

 

### We learned many things from this prototype:

- It was still heavy
- It was very wide
- To obligatorily have a direction mechanism 
- To check and follow the rules of the WRO 2024 competition
- It was very slow

After all this prototypes, we came to a conclusion: 

- We needed a robot that is:
  - light weighted
  - thin and short
  - have a direction mechanism and use a servomotor in it
  - follows the rules of the WRO 2024 competition
  - has 1 dc motor who makes both wheels move simultaneously
  - Fast in speed

So with this in mind, we built our final robot, Terreneitor, who has all of this characteristics and more.

(As stated at the beginning of this directory, if you want to know more about our final robot, check the other folders like:`vehicle photos` folder, the `build` folder, etc. You can also read the README of this repository since we mainly talk about our final robot there and in the other folders except for this one).

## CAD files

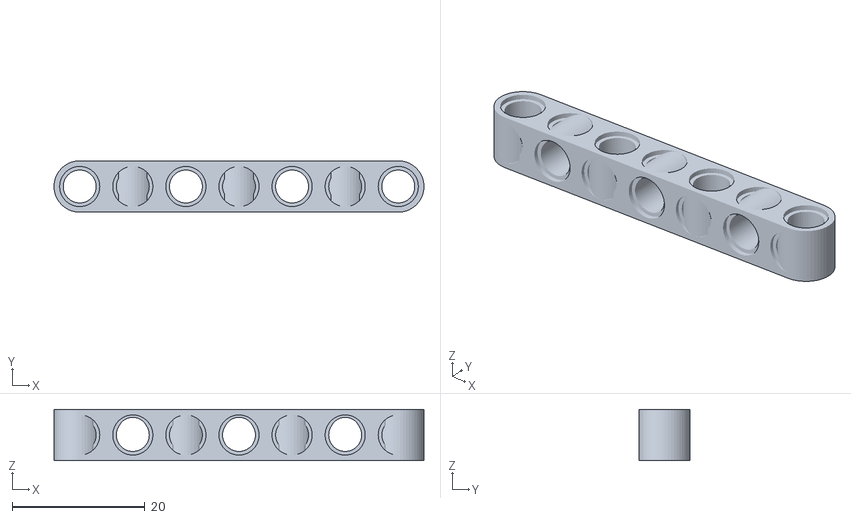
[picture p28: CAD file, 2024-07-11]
⚒️ Mobility management/3D printed model of beam.stl
55.8 x 7.75 x 7.75

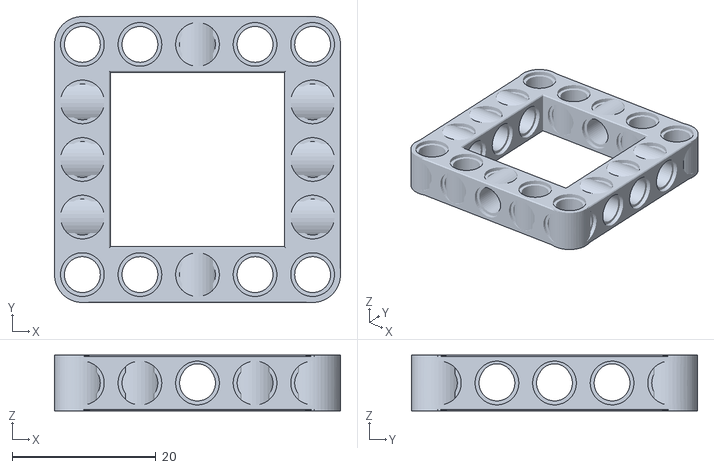
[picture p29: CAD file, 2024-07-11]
⚒️ Mobility management/3D printed model of beam frame.stl
39.8 x 39.8 x 7.75

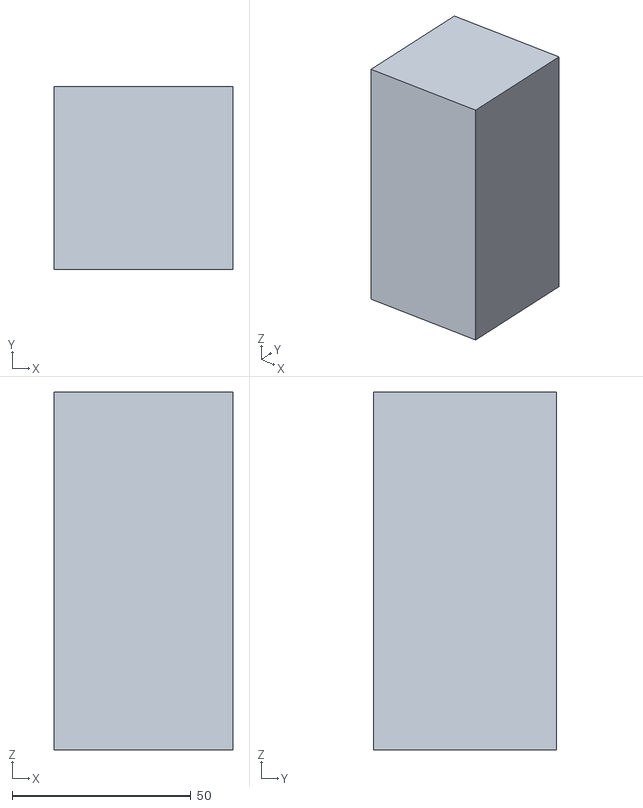
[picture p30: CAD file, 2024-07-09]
⚒️ Mobility management/3D printed model of obstacle.stl
50.0 x 51.0 x 100.0

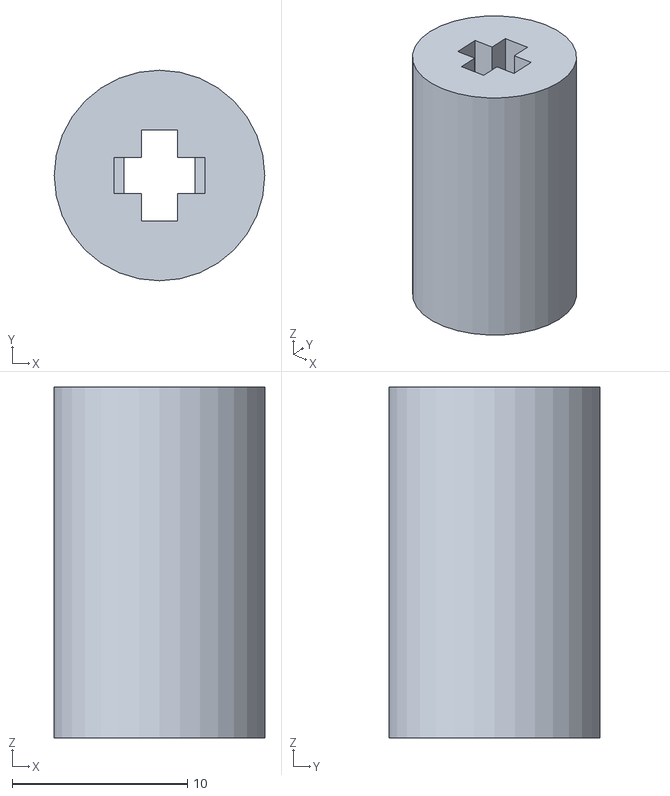
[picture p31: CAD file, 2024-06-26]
⚒️ Mobility management/3D model of the adapter .stl
12.0 x 12.0 x 20.0

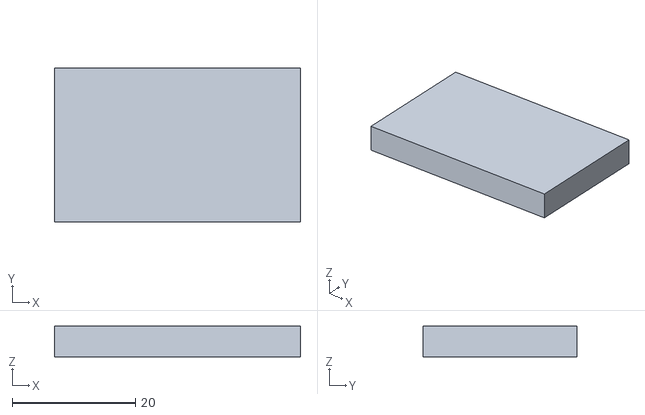
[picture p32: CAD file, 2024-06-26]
⚒️ Mobility management/3D model of blue piece.stl
40.0 x 25.0 x 5.00

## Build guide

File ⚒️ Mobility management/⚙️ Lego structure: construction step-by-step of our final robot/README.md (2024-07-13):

# Lego structure: construction step-by-step of our final robot

In this directory you will find the instructions step-by-step to create our lego structure so you can build it too at home! It counts with 18 pages and 72 easy steps.

(we made this instructions using the official lego _BrickLink_ app)

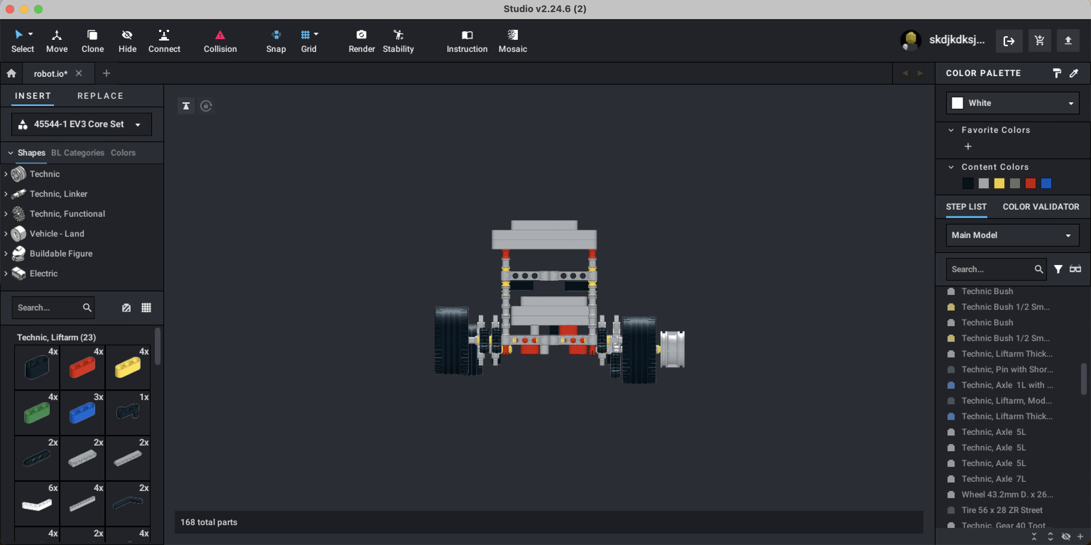
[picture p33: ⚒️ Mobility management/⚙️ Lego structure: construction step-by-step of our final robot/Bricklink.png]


We used different and a variety of lego pieces from different lego sets in order to create our original and unique robot. Here you will find only the guide to build the lego structure of our robot, therefore, the electrical components are not included in this guide.

The lego pieces we used for our robot are:



Now, you can find the guide in a file called "robot.pdf" or you can continue reading below:

# Let's start building together!

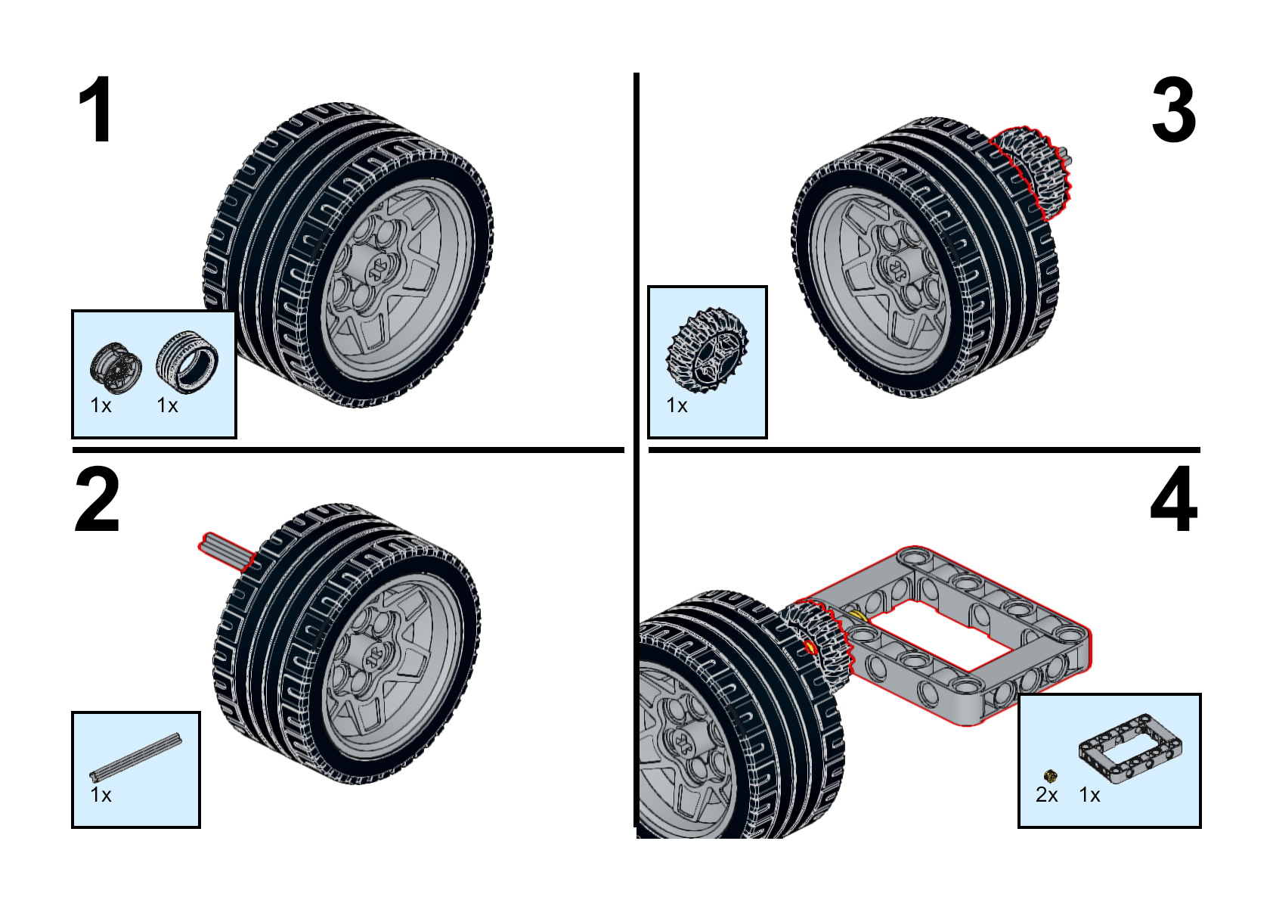
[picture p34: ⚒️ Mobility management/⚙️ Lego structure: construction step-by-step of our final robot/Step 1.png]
 
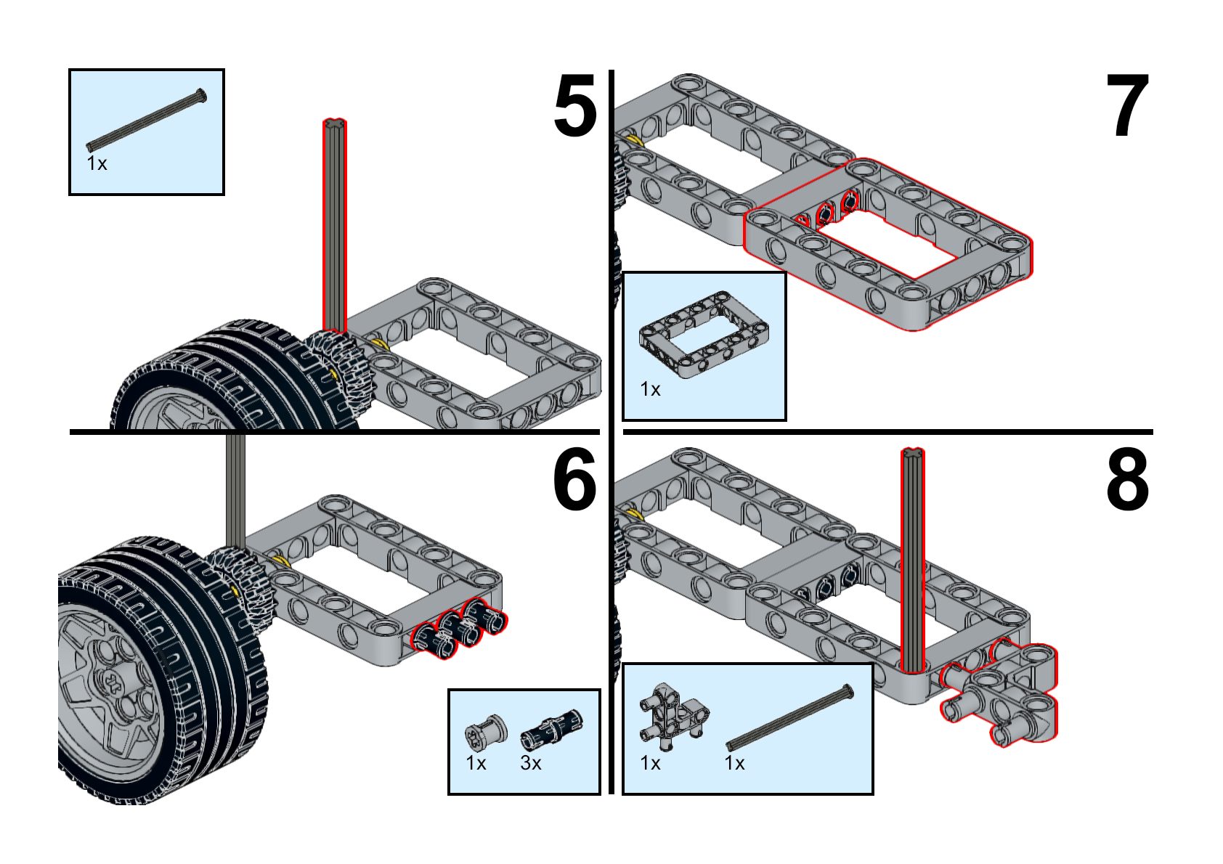
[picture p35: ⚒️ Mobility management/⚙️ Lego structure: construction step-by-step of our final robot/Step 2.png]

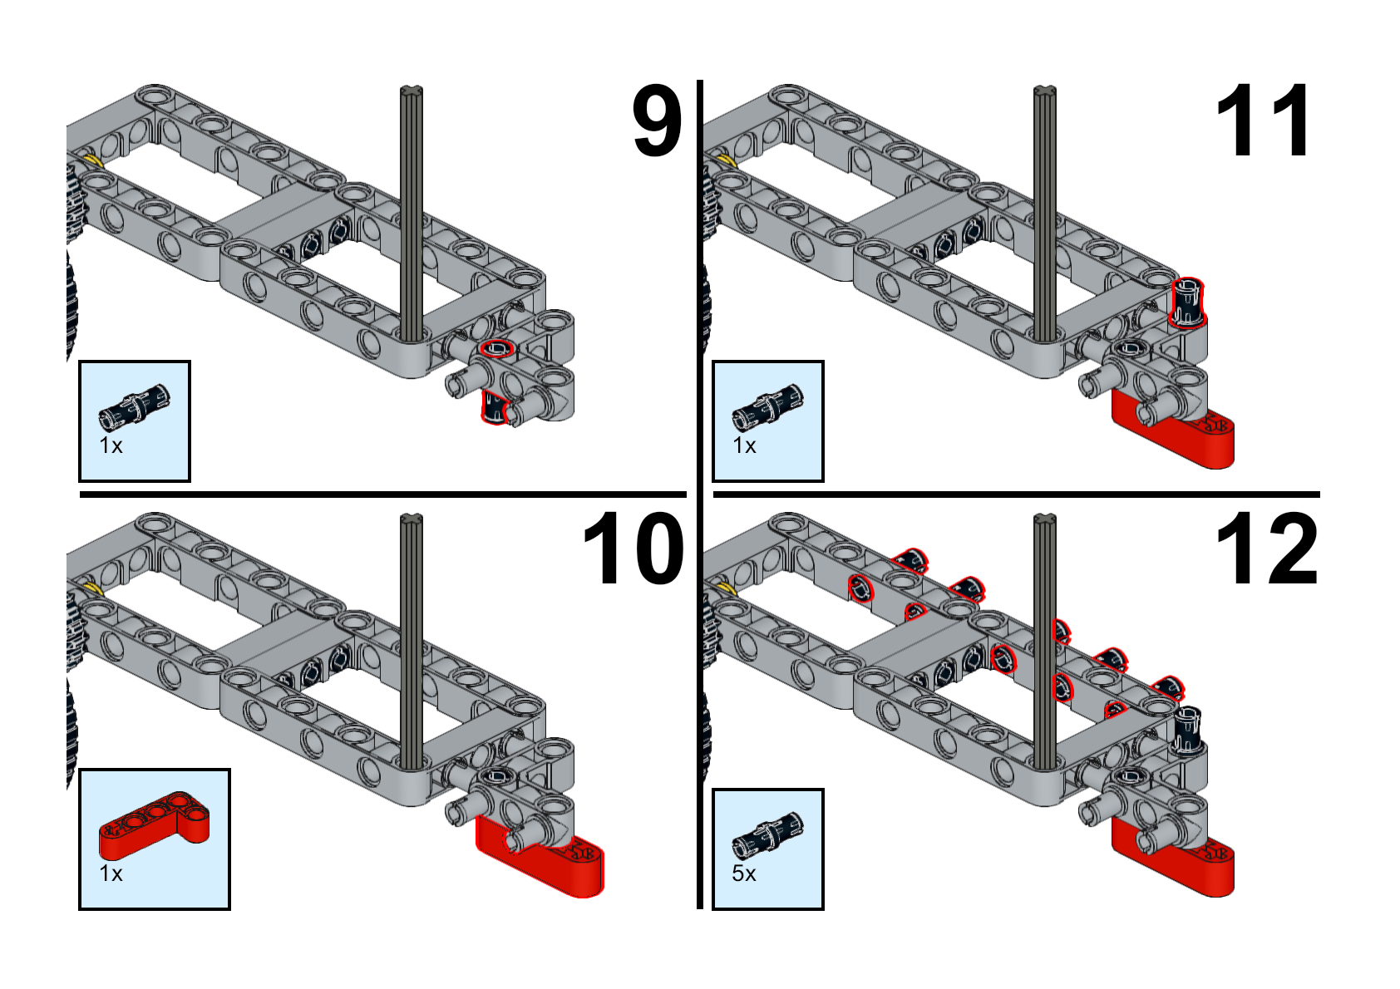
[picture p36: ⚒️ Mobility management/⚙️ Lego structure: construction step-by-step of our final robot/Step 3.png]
 
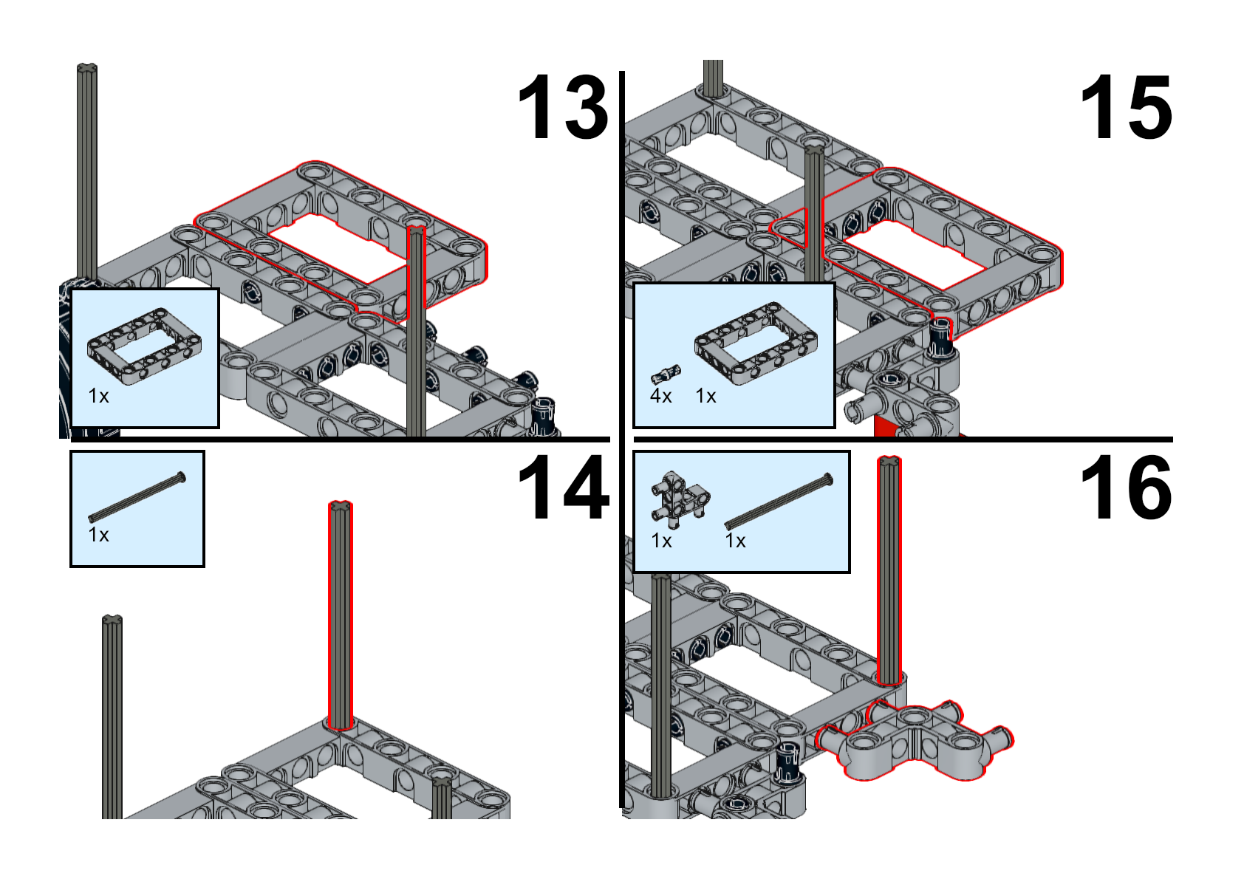
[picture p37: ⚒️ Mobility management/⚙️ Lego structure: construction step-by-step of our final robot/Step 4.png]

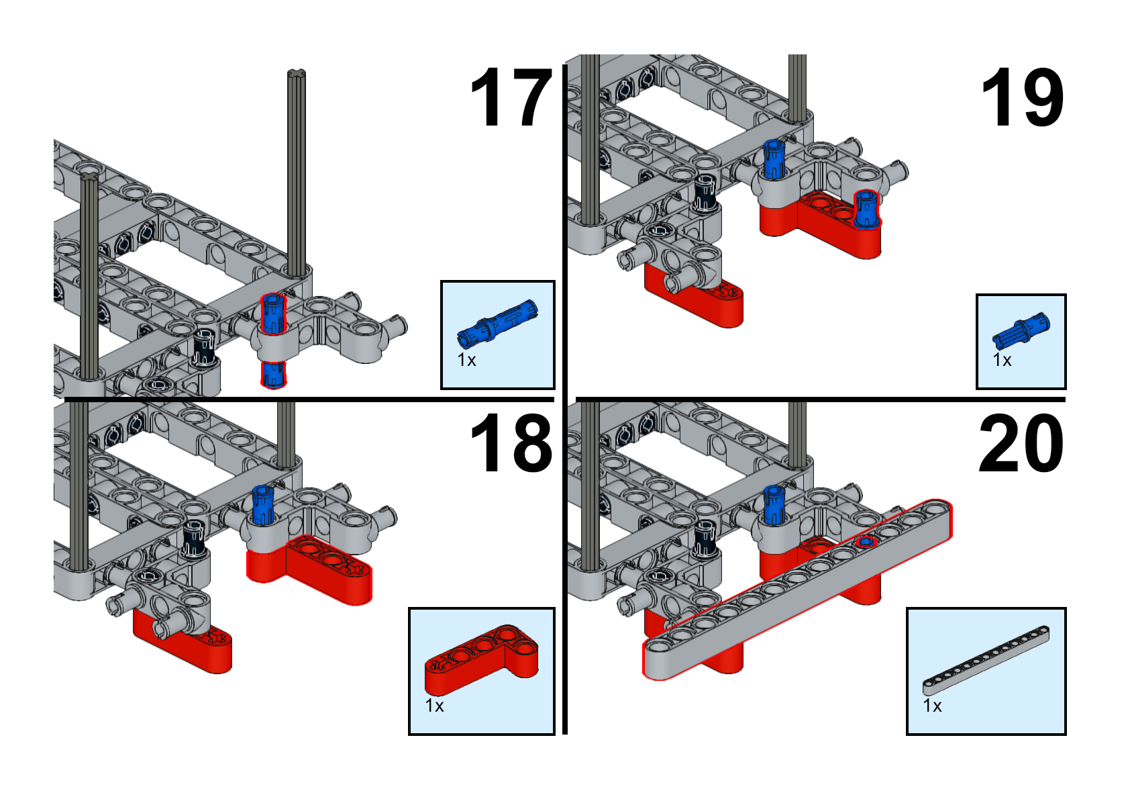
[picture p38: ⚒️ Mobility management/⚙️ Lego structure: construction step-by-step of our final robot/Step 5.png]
 
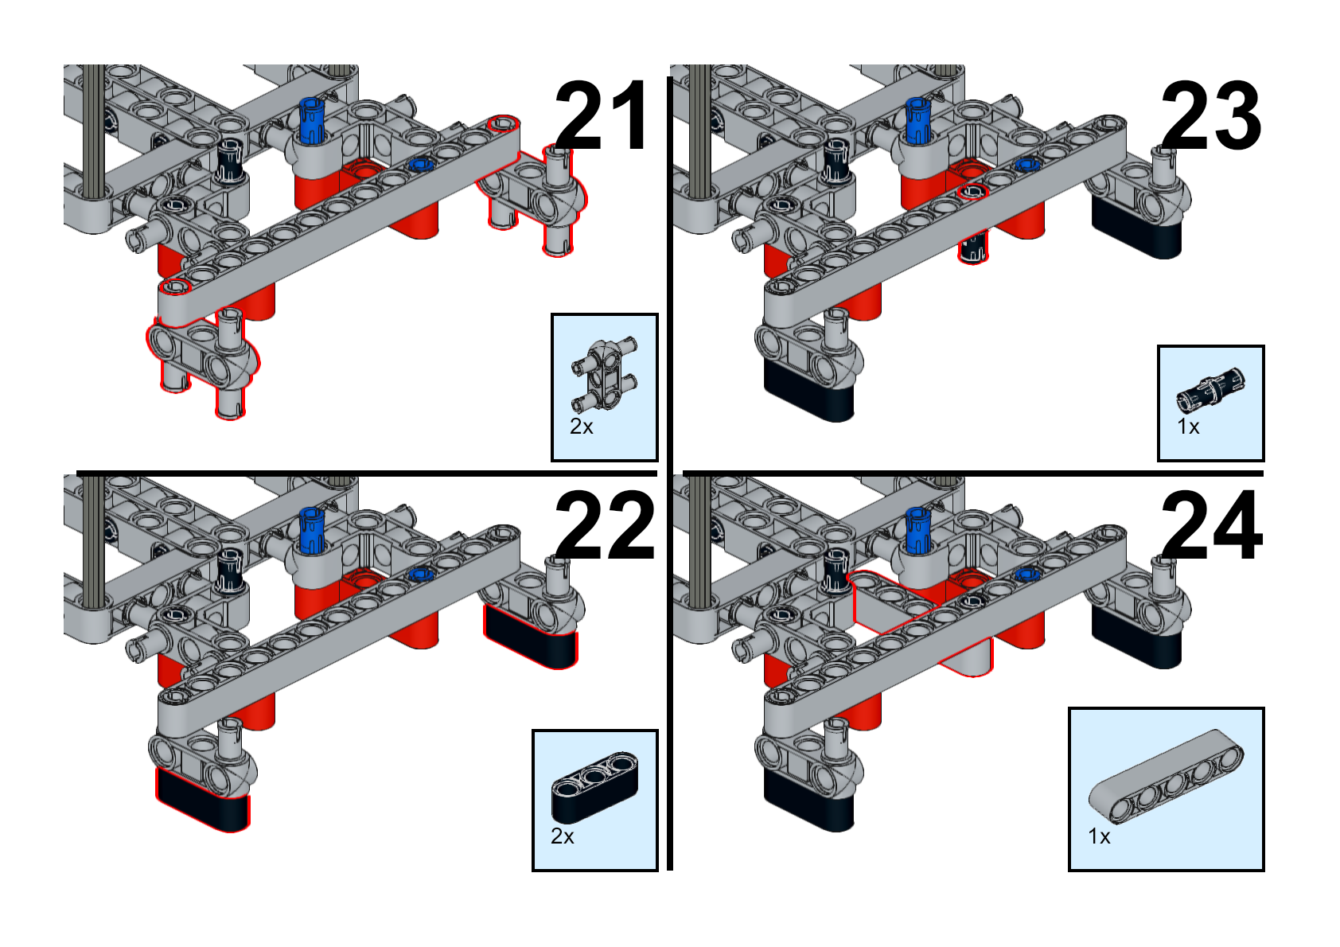
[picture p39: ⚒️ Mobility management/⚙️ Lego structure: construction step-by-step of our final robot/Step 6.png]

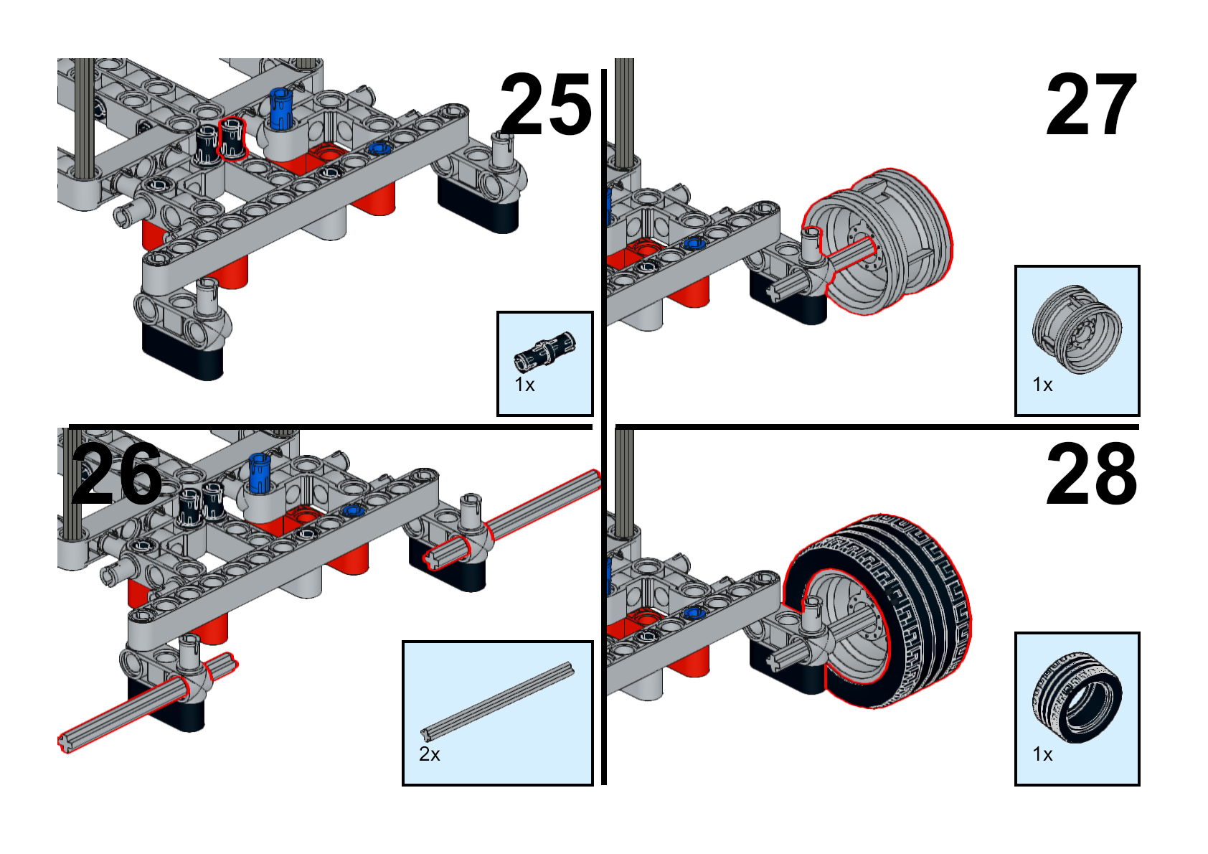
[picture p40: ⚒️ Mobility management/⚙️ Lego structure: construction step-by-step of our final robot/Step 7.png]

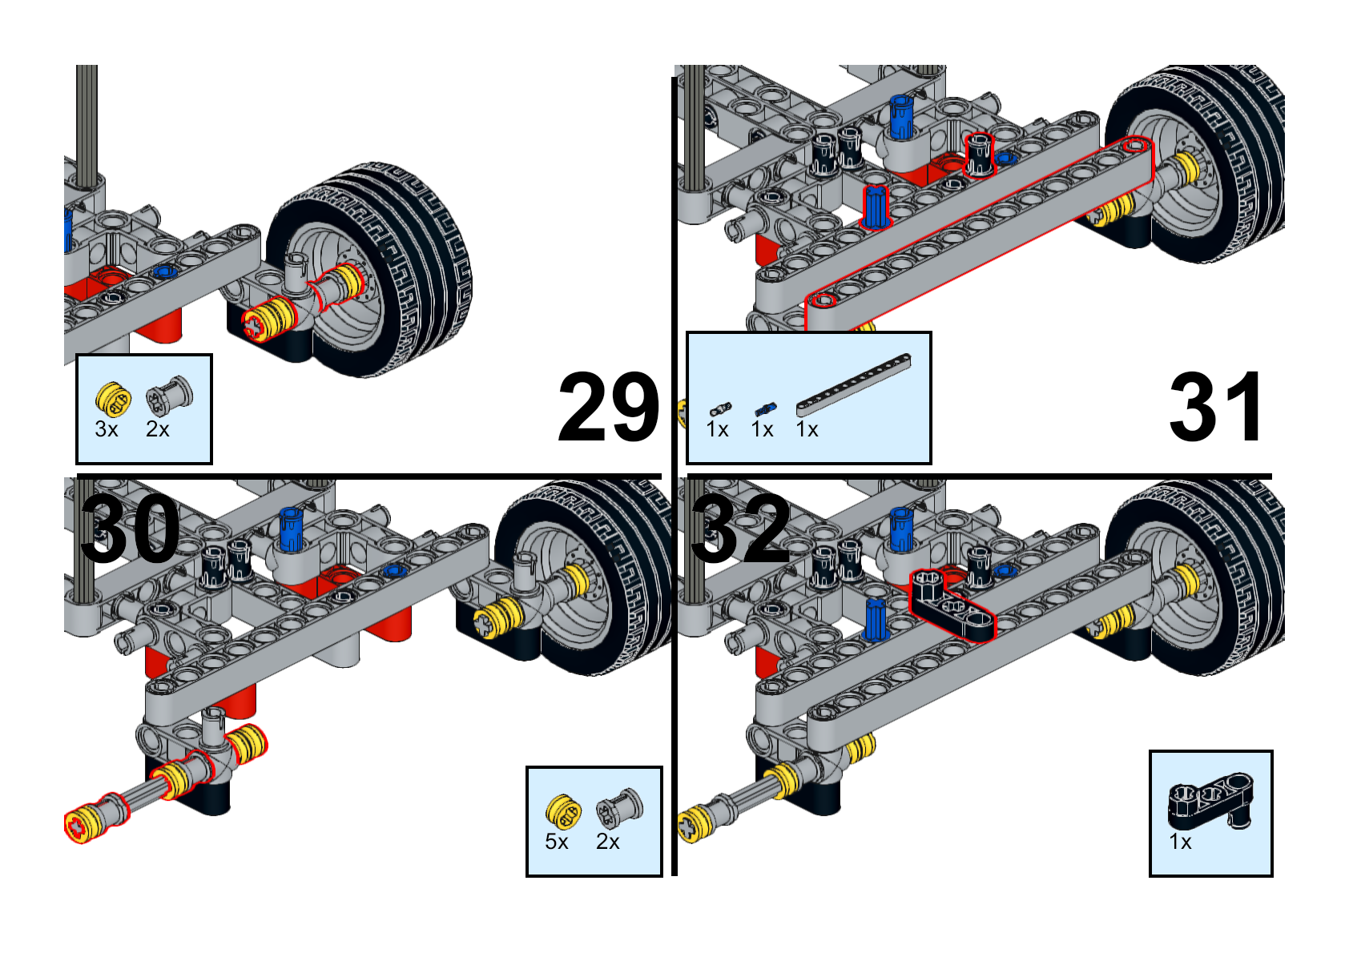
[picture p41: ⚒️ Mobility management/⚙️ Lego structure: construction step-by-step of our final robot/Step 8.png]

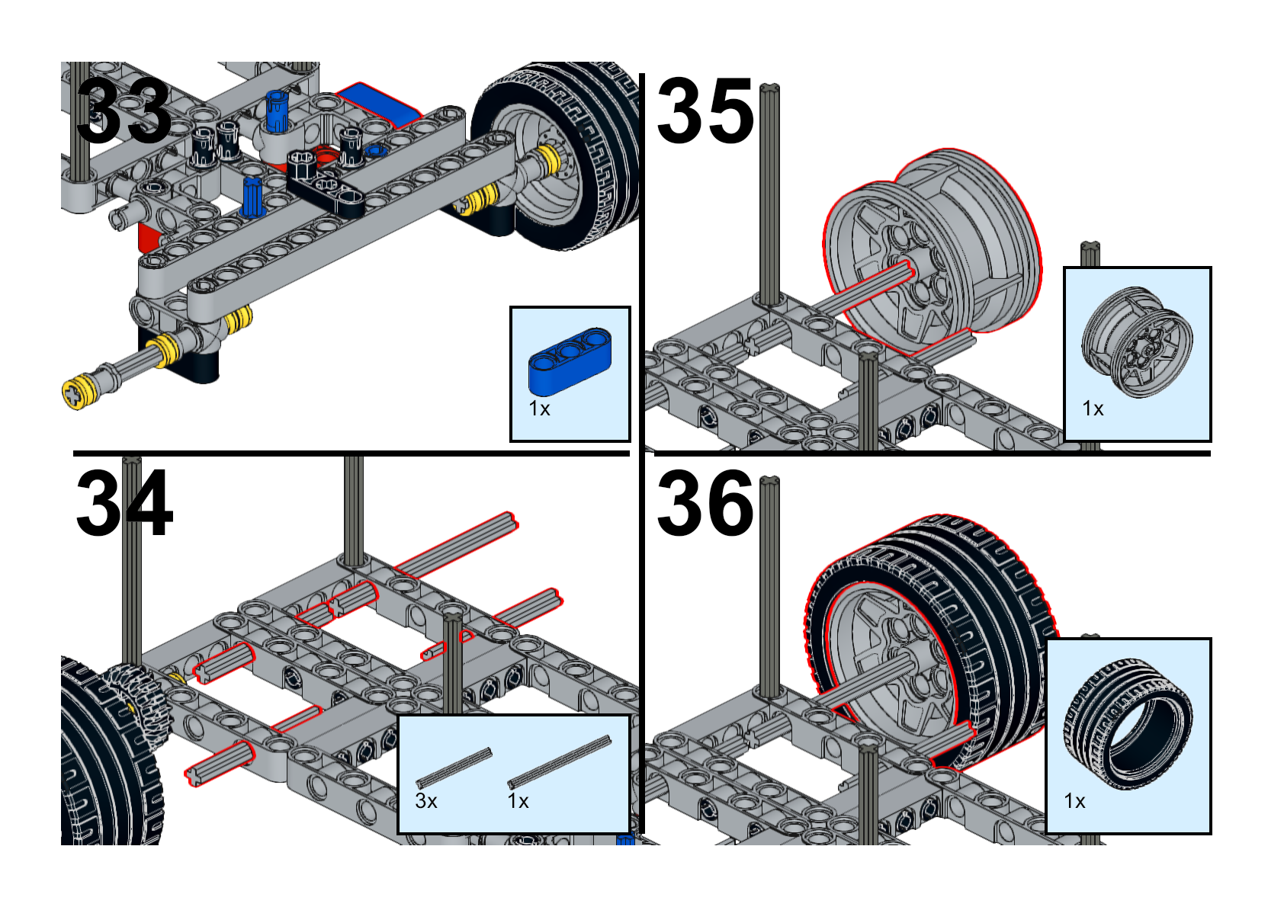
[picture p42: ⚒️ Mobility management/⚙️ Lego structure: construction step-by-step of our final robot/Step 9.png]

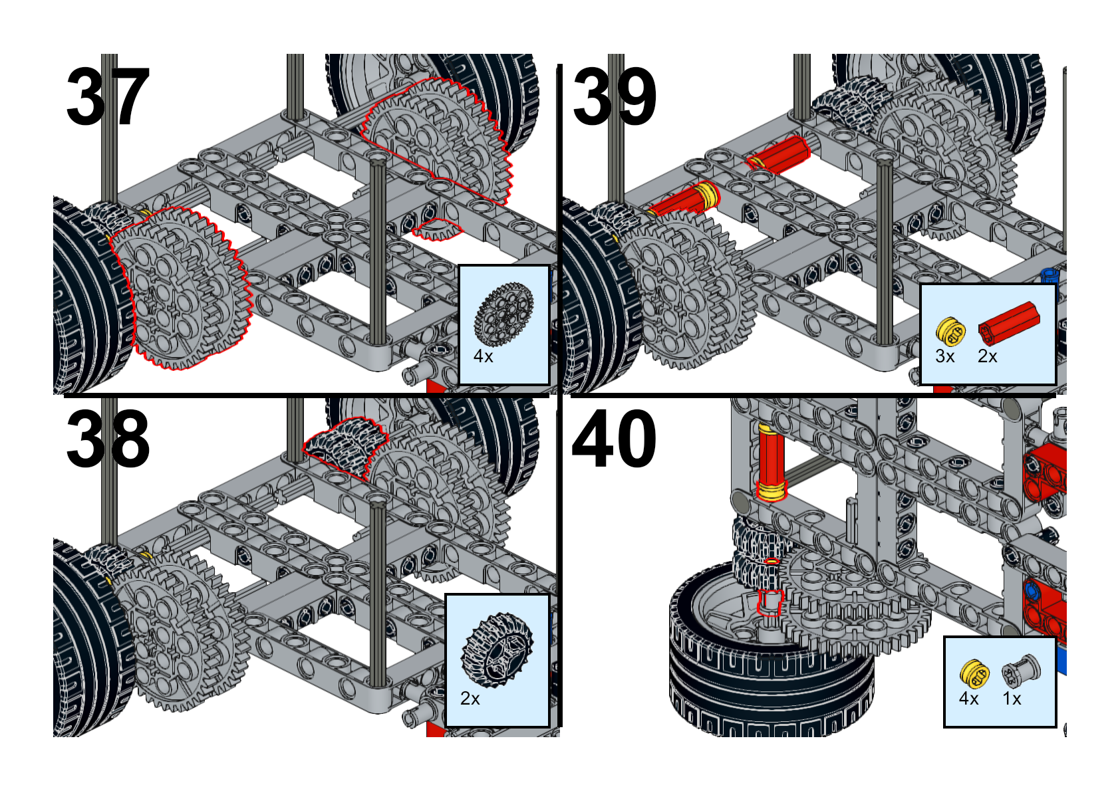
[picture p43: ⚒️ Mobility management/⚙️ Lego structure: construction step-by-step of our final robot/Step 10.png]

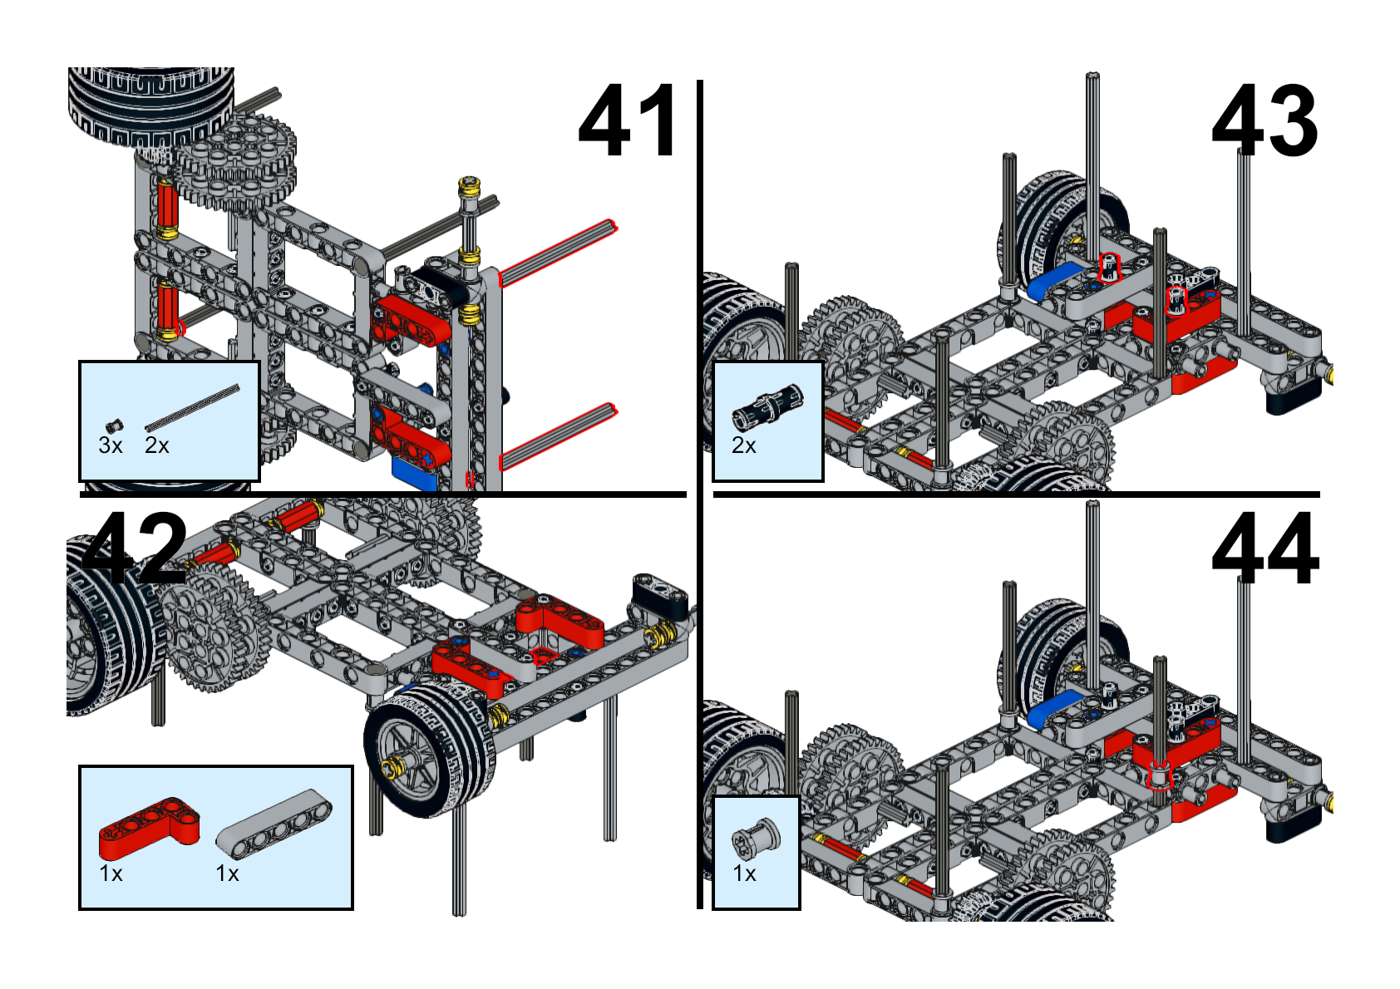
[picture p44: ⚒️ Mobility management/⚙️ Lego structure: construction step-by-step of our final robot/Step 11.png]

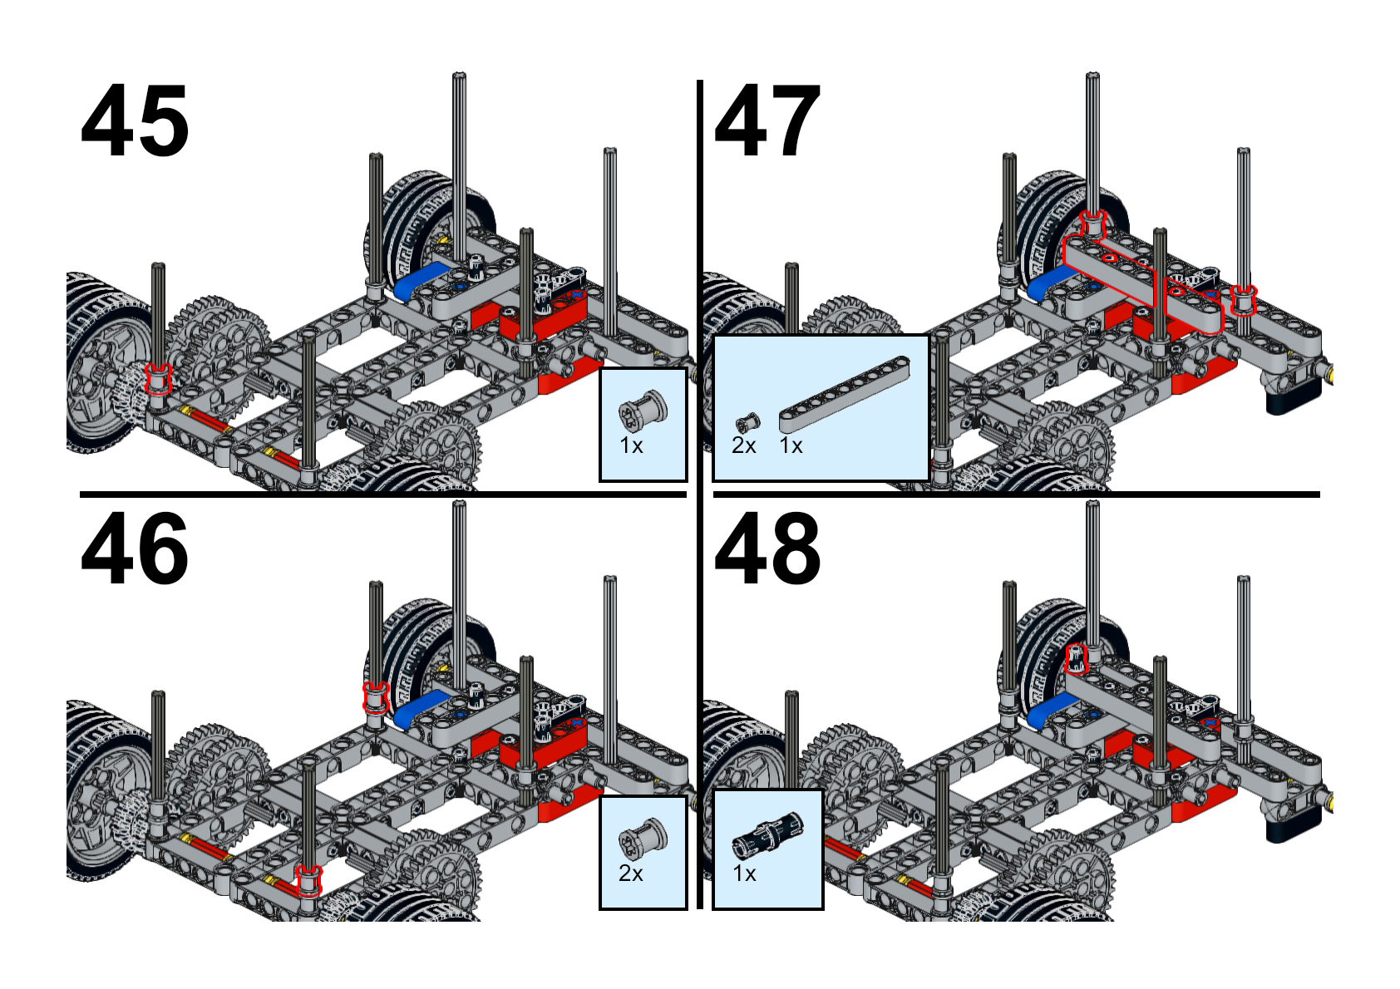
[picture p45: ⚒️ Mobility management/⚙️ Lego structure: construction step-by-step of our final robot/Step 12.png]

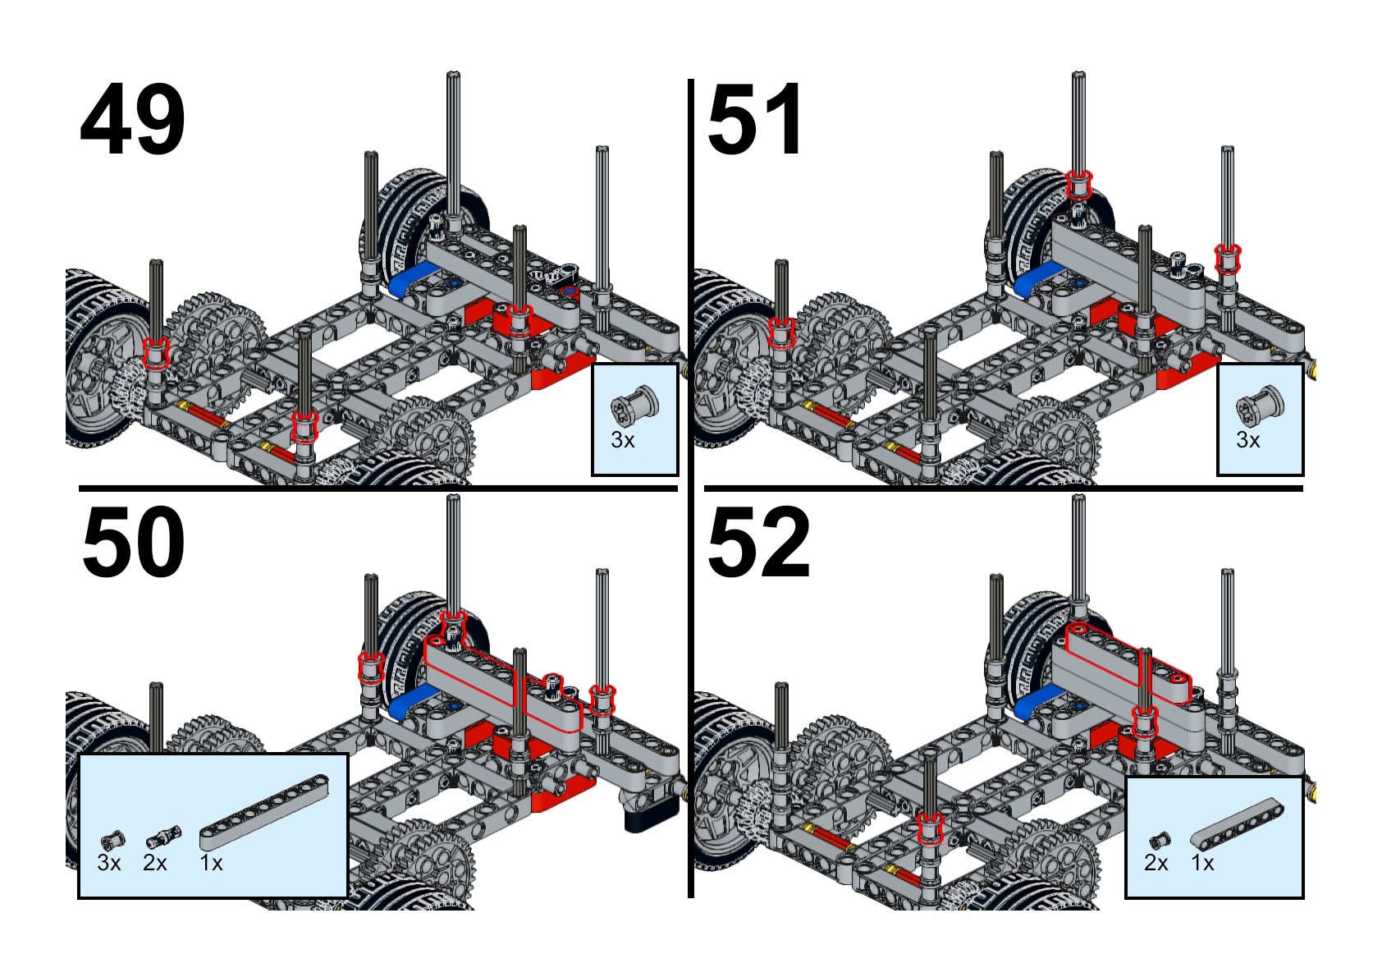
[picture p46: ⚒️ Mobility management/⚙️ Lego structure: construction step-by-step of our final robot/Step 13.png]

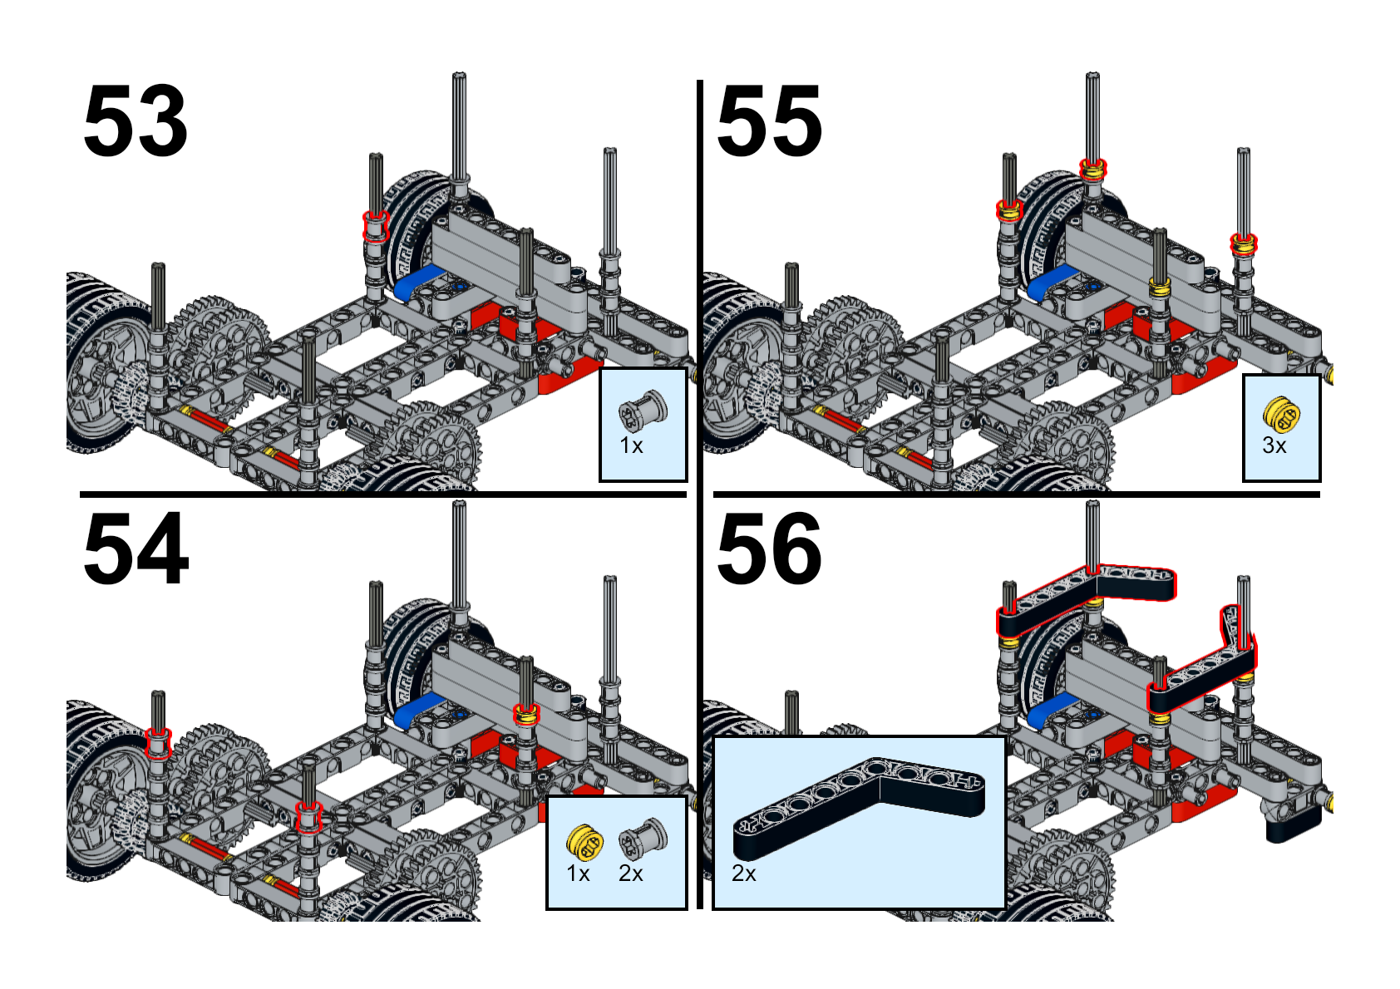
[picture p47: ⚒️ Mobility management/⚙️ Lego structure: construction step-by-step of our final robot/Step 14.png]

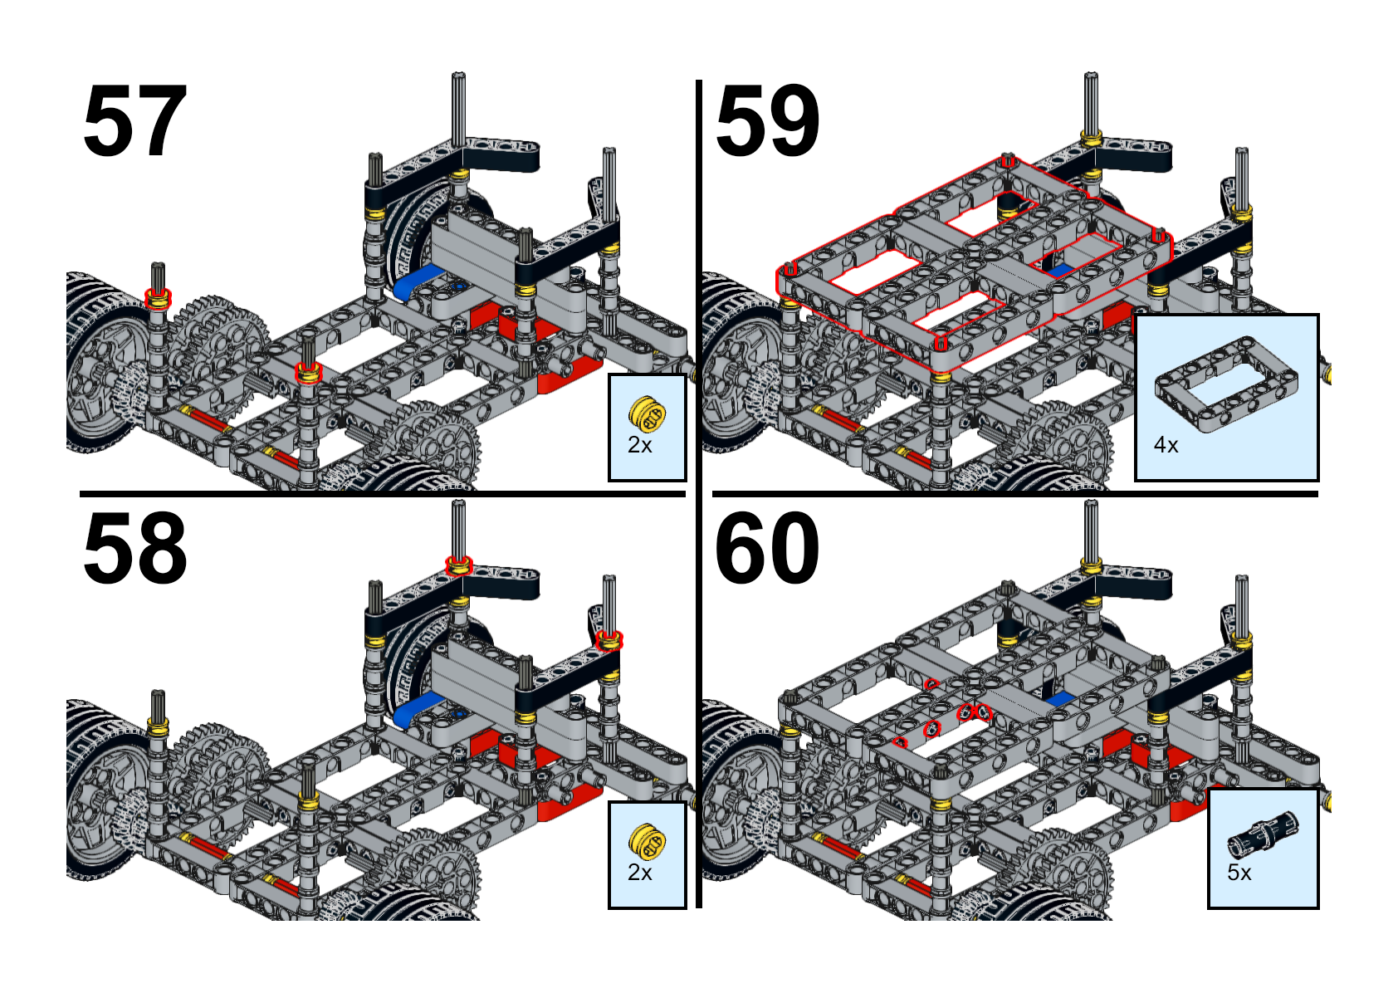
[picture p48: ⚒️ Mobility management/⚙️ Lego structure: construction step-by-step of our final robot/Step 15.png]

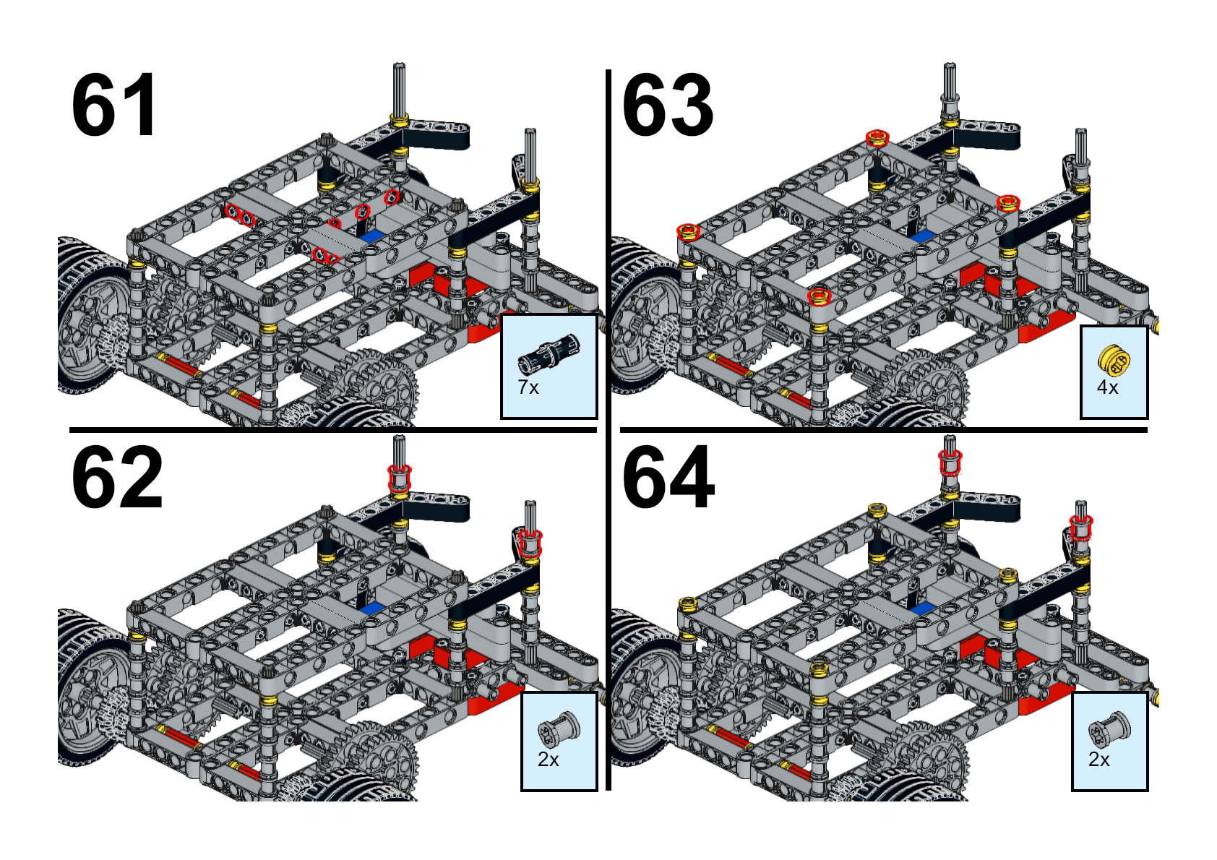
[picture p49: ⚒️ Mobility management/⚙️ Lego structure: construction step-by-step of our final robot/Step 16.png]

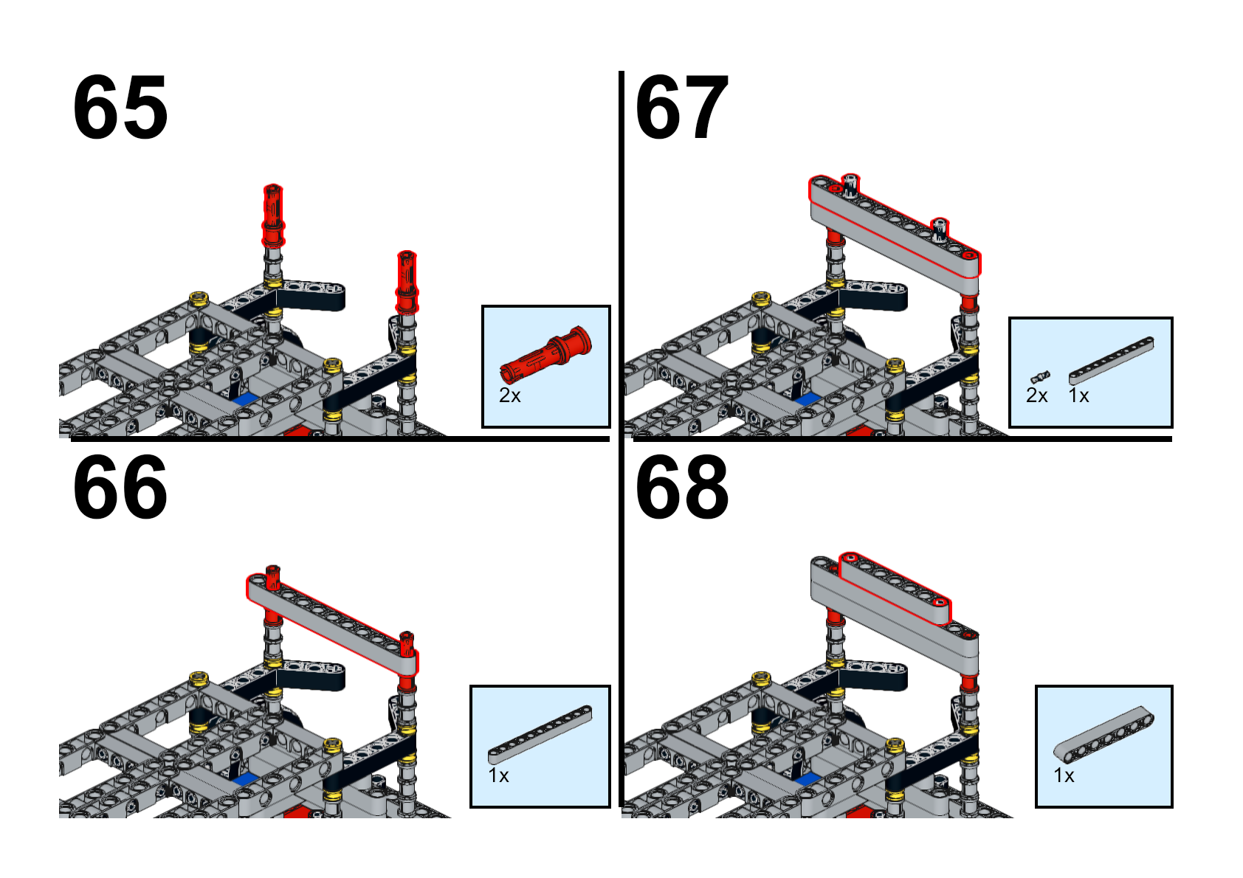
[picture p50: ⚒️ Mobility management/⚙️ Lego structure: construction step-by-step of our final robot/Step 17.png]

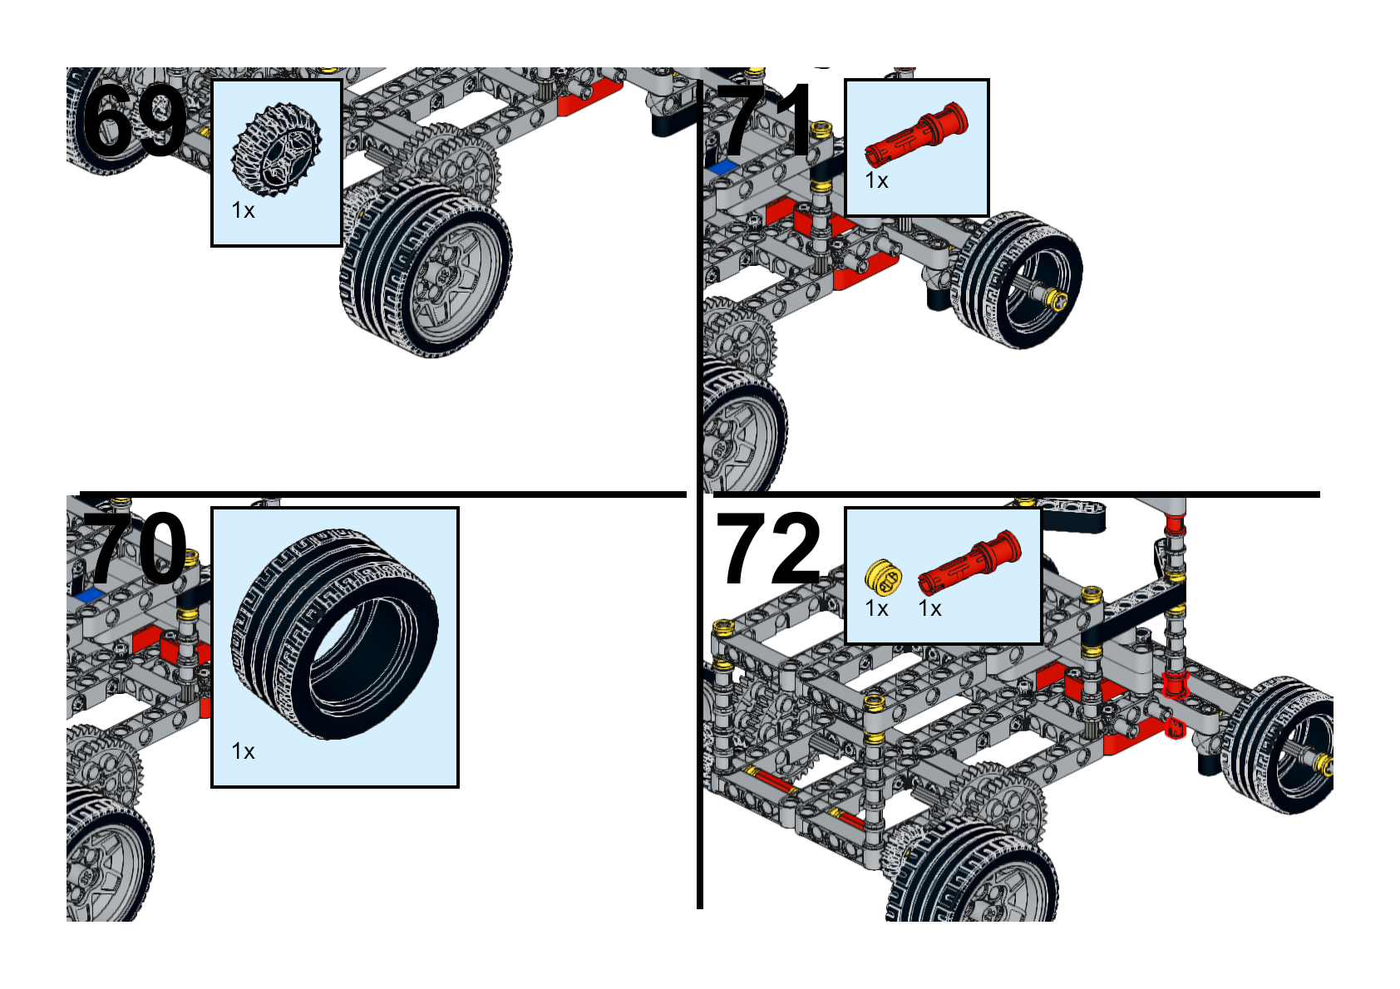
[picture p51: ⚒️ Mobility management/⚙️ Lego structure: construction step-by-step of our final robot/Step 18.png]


# And that's it, you now have an exact replica of our robot's lego structure!

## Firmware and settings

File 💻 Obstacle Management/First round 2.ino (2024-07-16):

#include <Servo.h> //Include libary to control servo motor functions
#include<Pixy2.h> //Include libary to control and unite pixy2 and pixymon
  
Servo servo; // Create a Servo object to control the servo motor  
Pixy2 pixy; // Create a Pixy2 object to interact with the Pixy2 camera  

int IN1 = 2;			// IN1 de L298N a pin digital 2
int IN2 = 3;			// IN2 de L298N a pin digital 3
int ENA = 5;			// ENA de L298N a pin digital 5
int VELOCIDAD=255;			// variable para almacenar valor de velocidad
int VELOCIDAD2=254;			// variable para almacenar valor de velocidad

int Servopin = 9; // Pin number for the servo motor  
int color; // Variable to store the detected color  
int go(37);// Variable to have the angle that makes the robot go forward
int left(9.2);//wVariable to have the angle that makes the robot go right 70
int right(58.19);//variable to have the angle that makes the robot to go left 10
int salto=0;


void setup() //function to declare variables
{  
  pinMode(5, OUTPUT); // Set pin 5 as an output for the DC motor  
  servo.attach(Servopin); // Attach the servo motor to the specified pin  
  Serial.begin(115200); // Initialize the serial communication at 115200 baud rate  
  pixy.init(); // Initialize the Pixy2 camera  
  pixy.setLamp(1, 1); // Set the Pixy2 camera's lamp to mode 1 (likely for color detection)
  pinMode(IN1, OUTPUT);		// pin 2 como salida
  pinMode(IN2, OUTPUT);		// pin 3 como salida	
  pinMode(ENA, OUTPUT);		// pin 5 como salida
  servo.write(0);
}  
  
void delay  (){
  delay(3000);
}
void loop() //function to create a loop
{
 
if(salto==0){// con la variable salto prendo los motores y calibro hacia el frente solo la primera vez que paso por aca 
  delay(2000);
  servo.write(37);
  delay(1000);
  analogWrite(ENA, VELOCIDAD);				// el valor de velocidad y aplica a ENA
  digitalWrite(IN1, LOW);				// IN1 en 0
  digitalWrite(IN2, HIGH);				// IN2 en 1
  salto= salto+1;
}
  
  
  int i; // Variable for loop counter   
  pixy.ccc.getBlocks(); // Get the blocks (objects with color) detected by the Pixy2 camera  
 
  
  if (pixy.ccc.numBlocks) // Check if any blocks (objects) were detected 
  {  
    
      Serial.println(pixy.ccc.numBlocks);// it tells you how many colors it sees 
      servo.write(go); // Set the servo motor to a position of 39 degrees, which in our robot means going straight forward
      color=pixy.ccc.blocks[i].m_signature;//Its saves on a variable the asignatures
       if (color==1) //If color(variable) is equal to signature #1 (which are the lines in color orange around the track)
      {
        Serial.println("NARANJA ");//prints when the pixy detects orange
      
        analogWrite(ENA, VELOCIDAD2);				// el valor de velocidad y aplica a ENA
        servo.write(right);
        delay(1630); //Wait for 800 milliseconds (0.8 seconds) 
        servo.write(go); // Set the servo motor to a position of 39 degrees, which in our robot means going straight forward
        delay(500);//delay one second
      }

      else if (color==2) //If color (variable) is equal to signature #2 (which are the lines in color blue around the track)
      {
        
        Serial.println("AZUL ");//prints when the pixy detects blue
        analogWrite(ENA, VELOCIDAD2);
        servo.write(left); // Set the servo motor to a position of 13 degrees, which in our robot means turning left
        delay(1650);//Wait for 800 milliseconds (0.8 seconds) 
        servo.write(go); // Set the servo motor to a position of 39 degrees, which in our robot means going straight forward
        delay(500);//delay one second
      }
  }
  Serial.println("NADA ");//Print when the pixy doesnt detect nothing 
  analogWrite(ENA, VELOCIDAD);
  servo.write(go); // Set the servo motor to a position of 39 degrees, which in our robot means going straight forward

} 

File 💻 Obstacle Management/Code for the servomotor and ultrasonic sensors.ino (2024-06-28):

#include <Servo.h>


Servo servo;

int ServoPin = 3;

int trigPin1 = 13;
int echoPin1 = 10;

int trigPin2 = 12;
int echoPin2 = 9;

int trigPin3 = 11;
int echoPin3 = 8;



void setup() {
  servo.attach(ServoPin);

  Serial.begin (9600);
  pinMode(trigPin1, OUTPUT);
  pinMode(echoPin1, INPUT);
 
  pinMode(trigPin2, OUTPUT);
  pinMode(echoPin2, INPUT); 
 
  pinMode(trigPin3, OUTPUT);
  pinMode(echoPin3, INPUT);
 
 
}

void firstsensor(){ // This function is for first sensor
  int duration1, distance1;
  digitalWrite (trigPin1, HIGH);
  delayMicroseconds (10);
  digitalWrite (trigPin1, LOW);
  duration1 = pulseIn (echoPin1, HIGH);
  distance1 = (duration1/2) / 29.1;

      Serial.print("1st Sensor: ");
      Serial.print(distance1); 
      Serial.print("cm    ");

  if (distance1 > 50) {  
    delay(500);
    servo.write(155);
   delay(800);
   servo.write(90);
  } else {
    
  }   
}
void secondsensor(){ // This function is for second sensor
    int duration2, distance2;
    digitalWrite (trigPin2, HIGH);
    delayMicroseconds (10);
    digitalWrite (trigPin2, LOW);
    duration2 = pulseIn (echoPin2, HIGH);
    distance2 = (duration2/2) / 29.1;
 
      Serial.print("2nd Sensor: ");
      Serial.print(distance2); 
      Serial.print("cm    ");
  
    if (distance2 > 50) {  
      delay(500);
      servo.write(0);
      delay(800);
      servo.write(90);
    }
 else {
      
    }  
 
}
void thirdsensor(){ // This function is for third sensor
    int duration3, distance3;
    digitalWrite (trigPin3, HIGH);
    delayMicroseconds (10);
    digitalWrite (trigPin3, LOW);
    duration3 = pulseIn (echoPin3, HIGH);
    distance3 = (duration3/2) / 29.1;

      Serial.print("3rd Sensor: ");  
      Serial.print(distance3); 
      Serial.print("cm");
  
    if (distance3 < 10) {  // Change the number 
     
    }
 else {
      
    }  
}

void loop() {
Serial.println("\n");
firstsensor();
secondsensor();
thirdsensor();
delay(100);
}

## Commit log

2024-06-25 Rename eea83f39-47cc-4285-b75c-add5c5086a4d.JPG to first prototype.JPG
2024-06-25 Rename eea83f39-47cc-4285-b75c-add5c5086a4d.JPG to prototype 1.JPG
2024-06-26 Rename Prototypes and sketches/5c5fd1ed-f62f-49b9-be93-fe9eb539e2ff.jpeg to Inicial sketches.jpeg
2024-06-26 Rename Prototypes and sketches/5c5fd1ed-f62f-49b9-be93-fe9eb539e2ff.jpeg to First sketches.jpeg
2024-06-26 Rename eea83f39-47cc-4285-b75c-add5c5086a4d.jpeg to First prototype.jpeg
2024-06-26 Rename Code/asjs to 💻 Code /&/&/&ksks
2024-06-26 Rename 💻 Code /&/&/&ksks to 💻 Code /Lalaks
2024-06-26 Rename Blue piece .stl to 3D model of blue piece .stl
    [3D model of blue piece .stl]
2024-06-26 Rename 3D model of blue piece .stl to 3D model of blue piece.stl
    [3D model of blue piece.stl]
2024-06-26 Rename Photoroom_20240626_104133.jpeg to First prototype step 2 (cenital view).jpeg
2024-06-26 Rename First prototype.jpeg to First prototype step 1 (cenital view).jpeg
2024-06-26 Rename Photoroom_20240626_104259.jpeg to First prototype step 3 (front view).jpeg
2024-06-26 Rename Photoroom_20240626_104603.jpeg to First prototype step 4 (worm’s-eye view).jpeg
2024-06-26 Rename bbf99dce-37f5-4673-86bc-08703b46d3b3.jpeg to First prototype.jpeg
2024-06-26 Rename Photoroom_20240626_123502.jpeg to Second prototype (frontal view).jpeg
2024-06-26 Rename Photoroom_20240626_123612.jpeg to Second prototype (side view).jpeg
2024-06-26 Rename Second prototype (side view).jpeg to Second prototype (cenital view).jpeg
2024-06-26 Rename Photoroom_20240626_123917.jpeg to Second prototype (back view).jpeg
2024-06-26 Rename Photoroom_20240626_124223.jpeg to Second prototype (another front view).jpeg
2024-06-27 Rename sketch_mod3lo_1.ino to code for the motors of the second prototype.ino
2024-06-27 Rename 45040-dscn0624-400x300.jpg to Arduino cables.jpg
2024-06-27 Rename 51DcBu3ByOL._AC_UF1000,1000_QL80_.jpg to Yellow 9V dc motor.jpg
2024-06-27 Rename 599104-40.jpg to Gray 5V dc motor.jpg
2024-06-27 Rename hc-sr04-ultrasonic-sensor.png to ultrasonic sensor.png
2024-06-27 Rename A000066_03.front_934x700.jpg.jpg to Arduino Uno Rev3 Board.jpg.jpg
2024-06-27 Rename 3eb2500f-fbcb-4763-bcd8-6af7aabf64d9.jpeg to First prototype step 0.1.jpeg
2024-06-27 Rename Arduino .png to Arduino IDE.png
2024-06-28 Rename Untitled.ino to Code for three ultrasonic sensors.ino
2024-06-28 Create 👤🔧 Team photos
2024-06-28 Rename 5944e7a8-d19e-4e1d-9f5c-0e150e5afc96.jpeg to Circuit of the final robot 1
2024-06-28 Rename Circuit of the final robot 1 to Circuit of the final robot 1.jpeg
2024-06-28 Rename 8a001a69-4e94-4100-b654-9d466eba87c6.jpeg to Circuit of the final robot for the sensors 2.jpeg
2024-06-28 Rename Circuit of the final robot 1.jpeg to Circuit of the final robot for the sensors1.jpeg
2024-06-28 Rename Untitled.ino to Code for the servomotor and ultrasonic sensors.ino
2024-07-04 Rename Final robot (back view) 2 de tamaño mediano.png to Final robot (back view) 2.png
2024-07-04 Rename Final robot (cenital view) 2 de tamaño mediano.png to Final robot (cenital view) 2.png
2024-07-04 Rename Final robot (front view) 2 de tamaño mediano.png to Final robot (front view) 2.png
2024-07-04 Rename Final robot (side view) 2 de tamaño mediano.jpeg to Final robot (side view) 2.jpeg
2024-07-09 Rename Grand Uusam-Densor.stl to 3D printed model of obstacle.stl
    [3D printed model of obstacle.stl]
2024-07-09 Rename 🖨️ Models/Engineering Factor/jkjk to 🖨️ Models/k
2024-07-09 Create Power and Sense Management
2024-07-09 Rename Pictures (Team and vehicle)/jkjkj to 👤🚘 Pictures (Team and vehicle)
2024-07-09 Rename Flowchart diagram TNT.jpeg to Old flowchart diagram TNT.jpeg
2024-07-11 Rename uBeam9.Holes1b.5x5.Fancy.stl to 3D printed model of beam frame.stl
    [3D printed model of beam frame.stl]
2024-07-11 Rename uBeam8.Beam7.AltH.FancyLookTest.stl to 3D printed model of beam.stl
    [3D printed model of beam.stl]
2024-07-11 Rename Gear+axles.stl.zip to 3D printed model of gears.stl.zip
2024-07-12 Rename IMG_6108.jpeg to Photo of gears.jpeg
2024-07-12 Rename IMG_6109.jpeg to Photo of beam frames.jpeg
2024-07-12 Rename 8bbfcbc7-a46d-488d-bcf8-623ec264a81d.jpeg to 3D printers.jpeg
2024-07-12 Rename 35 sin título_20240712170603.png to Wiring diagram.png
2024-07-14 Rename FUNCIONA_pixy-servo.ino to First round.ino
